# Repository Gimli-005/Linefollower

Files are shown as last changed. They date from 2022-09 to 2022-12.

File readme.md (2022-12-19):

# LineFollower
<br />
afbeelding
<br />
  
## specifications
<br />
microcontroller: ATmega32PU
<br />
motors: 50:1 Micro metal gear motor HP 6V
<br />
h-bridge: DRV 8835 Dual motor
<br />
sensors: QTR 8A sensor array
<br />
batteries: 1860 batteries
<br />
wireless communication: AZDelivery HM-10 Bluetooth Wireless RF Transceiver Module RS232 Seriële TTL 
<br />
distance sensor - motors: 140 mm
<br />
weight: 300 g
<br />
speed: 0.54
<br />

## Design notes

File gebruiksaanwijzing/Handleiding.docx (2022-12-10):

Handleiding

Syntheseproject

Linefollower

Robbe Malfroot
PBA-EM-3AM
971841rm

1. Opladen / vervangen batterijen

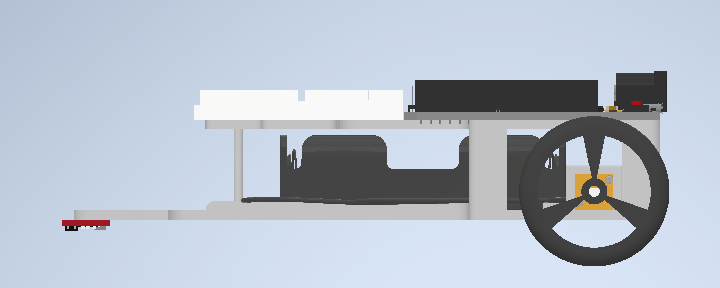
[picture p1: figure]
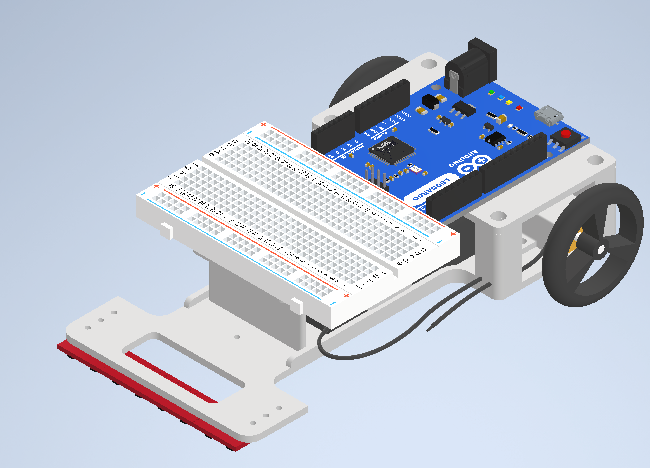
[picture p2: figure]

De batterijen kunnen vervangen worden door het bovenstaande arduino ondersteunig los te te koppelen. Waarbij we dan de batterijhouder van de linefollower kunnen halen. Om indien nodig de batterijen te vervangen. De batterijen kunnen opgeladen worden door een li-ion batterijlader, dat geschikt is voor 1860 batterijen op te laden.

2. Instellen HM-10 module

Het instellen van de HM-10 module gebeurt met AT-commando’s. Deze zijn terug te vinden in volgende link: https://people.ece.cornell.edu/land/courses/ece4760/PIC32/uart/HM10/DSD%20TECH%20HM-10%20datasheet.pdf

Installeer het programma “Bluetooth”. Open de Arduino IDE en open de seriële monitor. Hier plaatsen we de baudrate op 9600. Daarna stellen we de HM-10

module in met volgende commando’s:

- AT
- Controleert connectie: antwoord “OK”
- AT+NAME<uw naam> o Wijzigt naam naar “uwnaam”: antwoord “OK<uwnaam>”
- AT+BAUD<nummer>
- Wijzigt baudrate (voor ons naar nummer 4:9600): antwoord “OK<nummer>”
- AT-PIN<pincode> o Wijzigt pincode: antwoord “OK<pincode>”
- AT+RESET o Resets bluetooth module

Hierna is de MM-10 module ingesteld naar jouw voorkeur en klaar voor gebruik.

3. Verbinden bluetooth

Het verbinden met bluetooth gebeurd met de bluetooth app en de linefollower. Dit kan enkel nadat de bluetooth module is ingesteld bij stap 5.

Voor het instellen van HM-10 module gebeurt in volgende stappen:

1. Installeer de app op uw Android toestel via play store en type: Serial Bluetooth Terminal in.

2. Voorzie de linefollower van spanning

3. Verbind het Android toestel met de linefollower via bluetooth

a. Zoek hierbij naar de naam die je hebt ingesteld

b. Indien nodig, geef de code in die je hebt ingesteld

4. Open de Serial Bluetooth Terminal op het Android toestel

5. Ga naar “devices”

6. Druk op de ingestelde naam van jouw bluetooth module

a. Indien nodig, geef de code in die je hebt ingesteld

7. Ga naar “terminal”

8. Druk op het connect icoon rechts boven

a. In de terminal verschijnt:

i. Connecting…

ii. Connected

9. Hierna is de connectie bevestigd

10. Onderaan kunnen nu commando’s getypt worden en verzonden met het pijltje erna

a. De verzonden commando’s verschijnen in de terminal

b. Ook de antwoorden zullen te lezen zijn in de terminal

4. Gebruik van de linefollower

Eenmaal je verbonden bent met bluetooth door middel van stap 3 (Verbinden met bluetooth) kan je via bluetooth communiceren met de linefollower.

Daarna voor de linefollower te laten rijden moet eerst alle parameters ingesteld worden. Als de

sensoren moeten gekalibreerd worden.

Kalibreren

Voor de sensoren te kalibreren moet er in de seriële monitor via de computer of bluetooth module het commando worden getypt:

- “calibrate white”
- “calibrate black”

Indien het commando is doorgestuurd zal deze de waarden opslaan. Zorg er wel voor dat de linefollower op een volledige witte ondergrond staat om de witte waarden op te slaan en bij de zwarte waarden op een volledige zwarte ondergrond staat.

Rijden

Nu kunnen de parameters worden doorgestuurd aan de hand van de commando’s. Met het commando: “run” zal de line follower starten met rijden. Bij het commando “stop” zal deze stoppen met rijden.

Indien een commando wordt doorgestuurd die fout geschreven is of onjuist is zal er een message

verschijnen dat deze niet gevonden is, dus er kan niets kapot gaan door een fout commando door te

sturen.

De commando’s dat kunnen gegeven worden in bluetooth module:

- “run”:

=> Starten met rijden (dit kan ook met de knop gedaan worden).

- “stop”:

=> Stoppen met rijden.

- “debug”:

=> Tonen van de ingestelde parameters met de waarden.

- “calibrate”:

=> Calibreren van de sensoren.

- “set cycle ‘waarde”:

=> Set cycle naar ‘waarde’ (waarde moet cijfer zijn).

- “set power ‘waarde”:

=> Set power naar ‘waarde’ (waarde moet cijfer zijn).

- “set diff ‘waarde”:

=> Set diff naar ‘waarde’ (waarde moet cijfer zijn).

- “set kp ‘waarde”:

=> Set kp naar ‘waarde’ (waarde moet cijfer zijn).

- “set ki ‘waarde”:

=> Set ki naar ‘waarde’ (waarde moet cijfer zijn).

- “set kd ‘waarde”:

=> Set kd naar ‘waarde’ (waarde moet cijfer zijn).

Ingestelde waarden:

Tijdens het testen van de linefollower kwamen men bij deze instellingen de beste waarden uit:

- Cycle time: 1300
- Kp: 15
- Ki: 0
- Kd: 0.25
- Diff: 0.2
- Power: 100

Dit leverde een resultaat op met een snelheid van 0.54 m/s. Hierbij gaat de linefollower de lijn volgen met de ingestelde parameters.

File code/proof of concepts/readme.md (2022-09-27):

# Proof of Concepts

Een proof of concept is een combinatie van minimale hard- en software om eenvoudig aan te tonen dat iets werkt.  
Proof of concepts kunnen enerzijds als eerste poging dienen om een bepaald onderdeel van het project werkend te krijgen. Anderzijds kunnen ze tijdens het debuggen van het finale project dienen als test om eventuele hardware problemen te elimineren bij onduidelijke problemen.
<br />  
<br />
Een proof of concept bestaat uit
* een elektronisch schema (indien van toepassing)
* minimale code om de voorop gestelde zaken te demonstreren
* minimale uitleg / aandachtspunten
<br />
De elektronische schakelingen van de proof of concepts komen bij voorkeur overeen met deze van de uiteindelijke linefollower, zodat de code zonder aanpassingen op het finale project kan draaien.

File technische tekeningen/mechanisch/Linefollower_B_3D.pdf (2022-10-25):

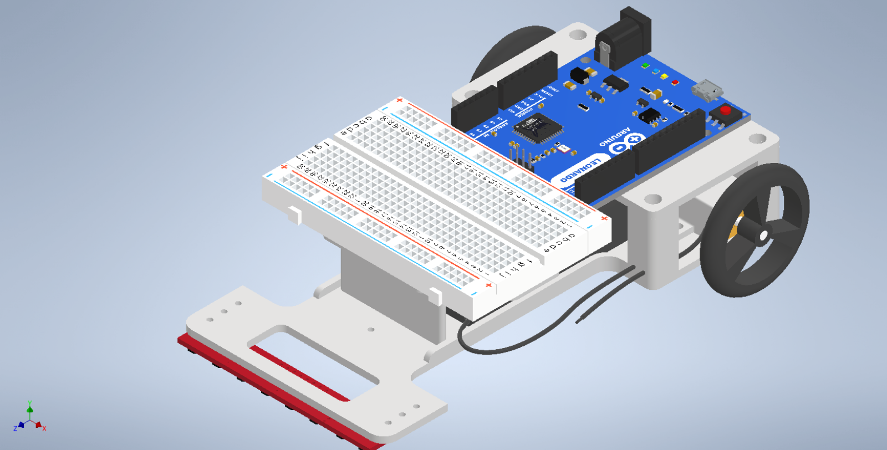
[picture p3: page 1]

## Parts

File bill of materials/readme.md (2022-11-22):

## bill of materials
<br />

|volgnummer|naam|omschrijving|nieuw/recup|kostprijs/stuk|aantal|subtotaal|
|---|----|---|---|---|---|---|
| 1| 50:1 Micro metal gear motor HP 6V  | | Nieuw | €20,41 |  2 | €40,82 |
| 2| QTR 8A Sensor array | | Nieuw | €10,18 | 2 | €20,36 |
| 3| Wheels 40*8mm  | | Nieuw | €5,06 | 2 | €10,12 |
| 4| Batterijen 18650  | | Nieuw | €15,09 |  6 | €15,09 |
| 5| Batterijhouder voor 18650  | | Nieuw |  €5,39 |  1 | €5,39 |
| 6| H-brug  DRV8835 | Voor besturing wielen |  Nieuw | €14,27 |  1 |  €14,27 |
| 7| Communicatie HC-05  | | Nieuw | €6,99 + €2,25  |  1 |  €9,25 |
| 8| Arduino Leonardo | | Nieuw | €25,52  | 1 | €25,52 |
| 9| Bouten M2/M5 | | recup | |  1 | |
| 10| Batterijlader 18650 | |  Nieuw | €15,02 |  1 | €15,02 |
| 11| Moeren M2/M5 | | recup | | 1 | |
| 13| printplaatje 5cmx7cm  | | nieuw | 1 | 1  | €0.99 |
| 14| Transportkosten | | | | | €36,00 |
| 15| | | | | | |
| 16| Totaal | | | | | €176,65 |

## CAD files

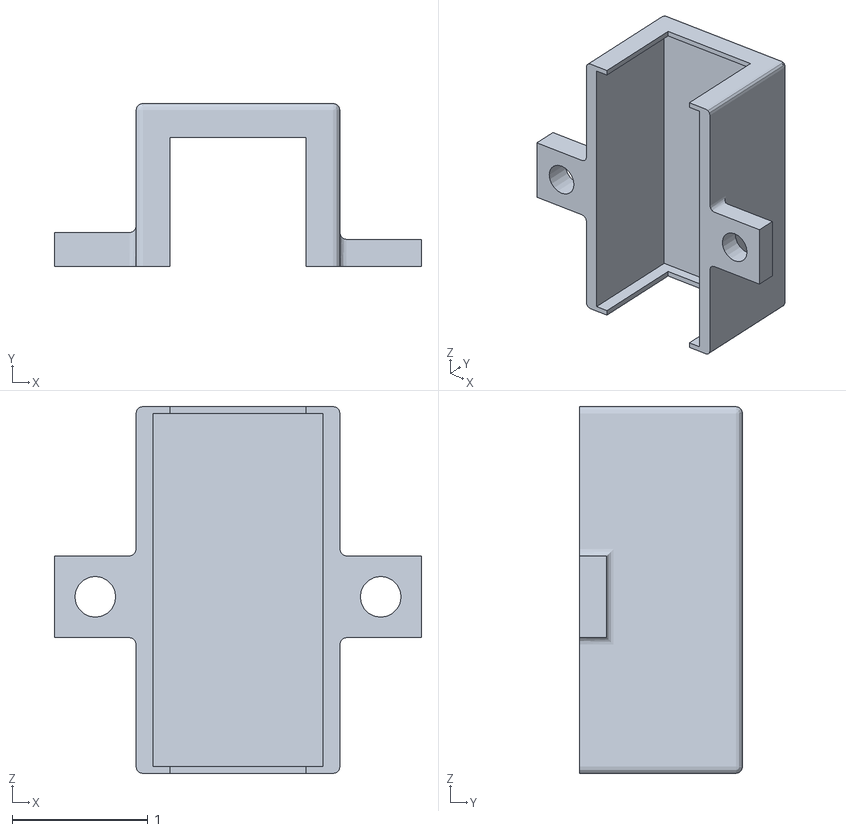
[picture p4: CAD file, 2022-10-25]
technische tekeningen/mechanisch/Ondersteuning motor.stl
2.70 x 1.20 x 2.70

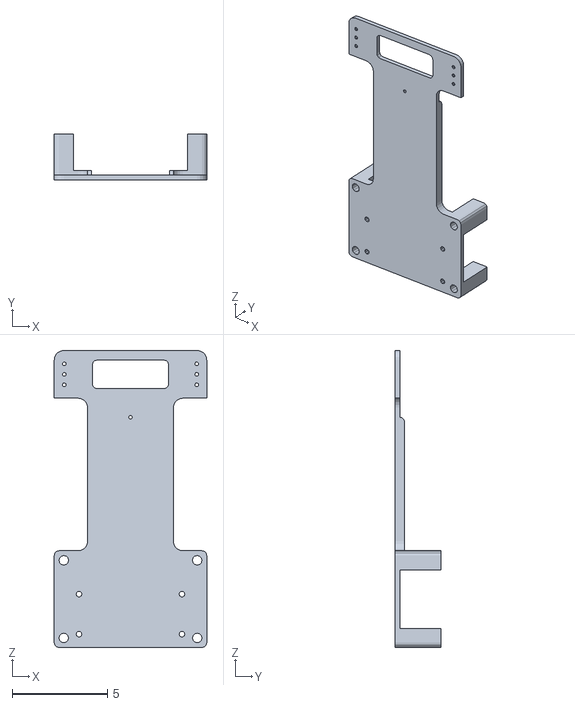
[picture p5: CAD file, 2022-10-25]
technische tekeningen/mechanisch/Chasis Linefollower_verbeterd.stl
8.00 x 2.40 x 15.6

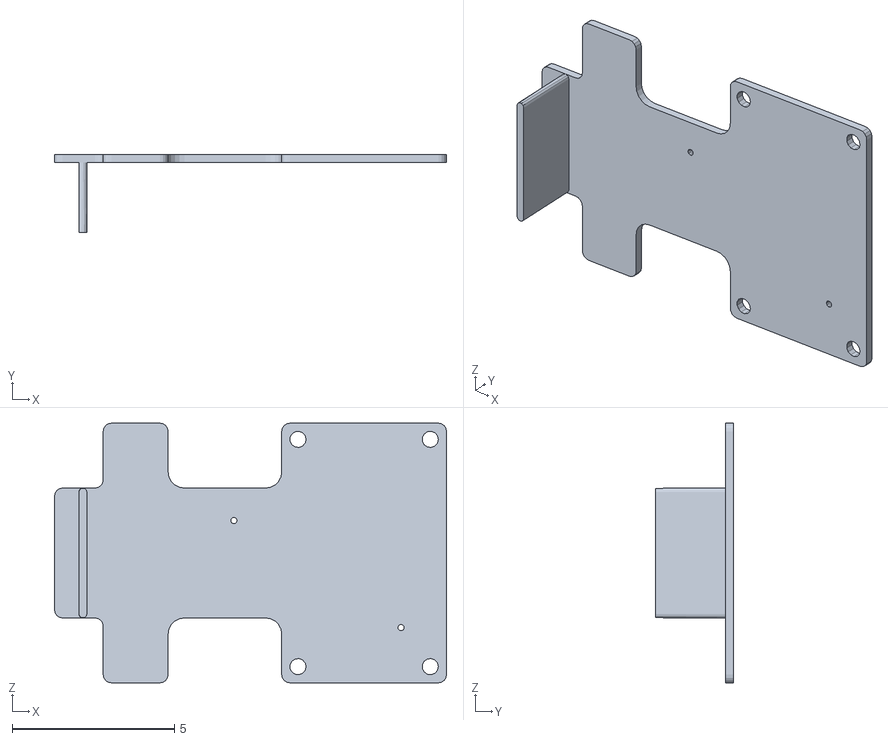
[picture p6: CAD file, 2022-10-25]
technische tekeningen/mechanisch/Arduino-ondersteuning.stl
12.1 x 2.40 x 8.00

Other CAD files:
technische tekeningen/mechanisch/Arduino-ondersteuning.ipt
technische tekeningen/mechanisch/Linefollower_B.idw
technische tekeningen/mechanisch/Samenstelling aandrijving.iam
technische tekeningen/mechanisch/Wiel.ipt
technische tekeningen/mechanisch/batteijhouder_1.ipt

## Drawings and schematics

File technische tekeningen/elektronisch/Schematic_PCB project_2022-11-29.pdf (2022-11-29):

## U1HC⁻05

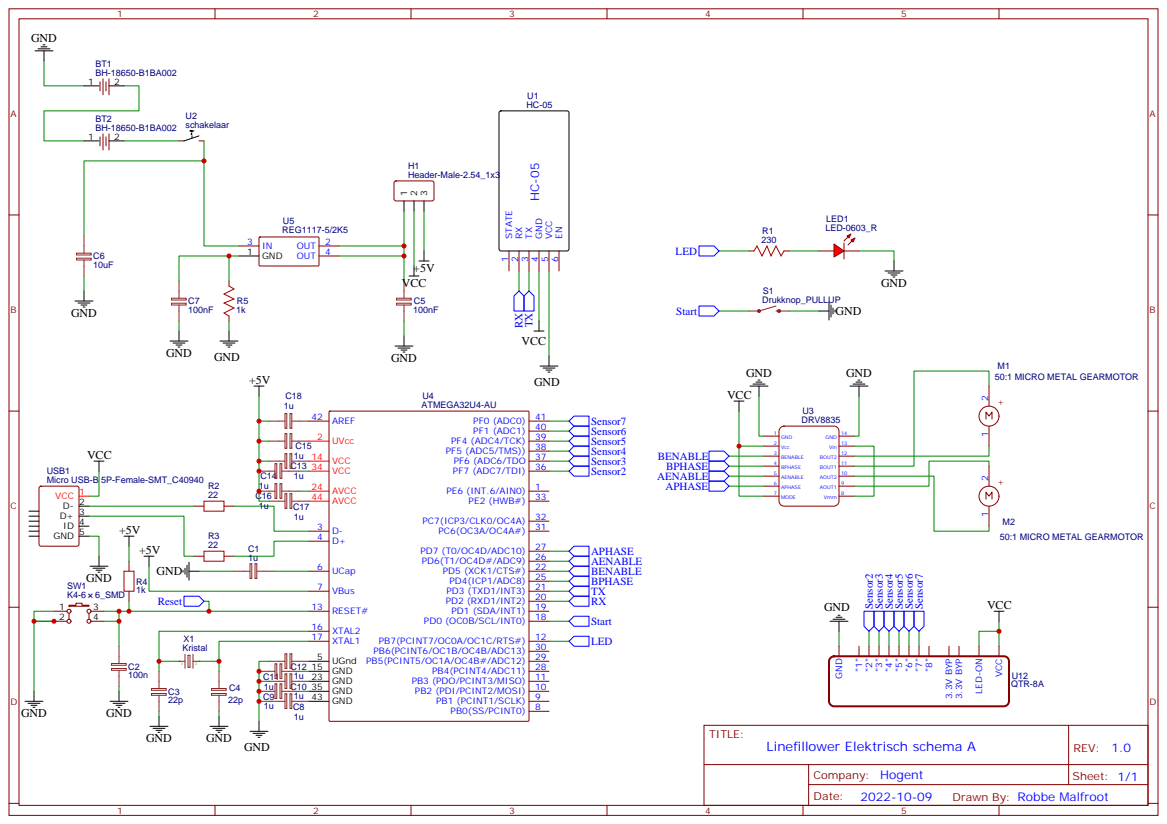
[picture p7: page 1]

PB7(PCINT7/OC0A/OC1C/RTS#) 12
PB2 (PDI/PCINT2/MOSI) 10 PB3 (PDO/PCINT3/MISO) 11 PB4(PCINT4/ADC11) 28 PB5(PCINT5/OC1A/OC4B#/ADC12) 29 PB6(PCINT6/OC1B/OC4B/ADC13) 30

Drawn By: Robbe Malfroot

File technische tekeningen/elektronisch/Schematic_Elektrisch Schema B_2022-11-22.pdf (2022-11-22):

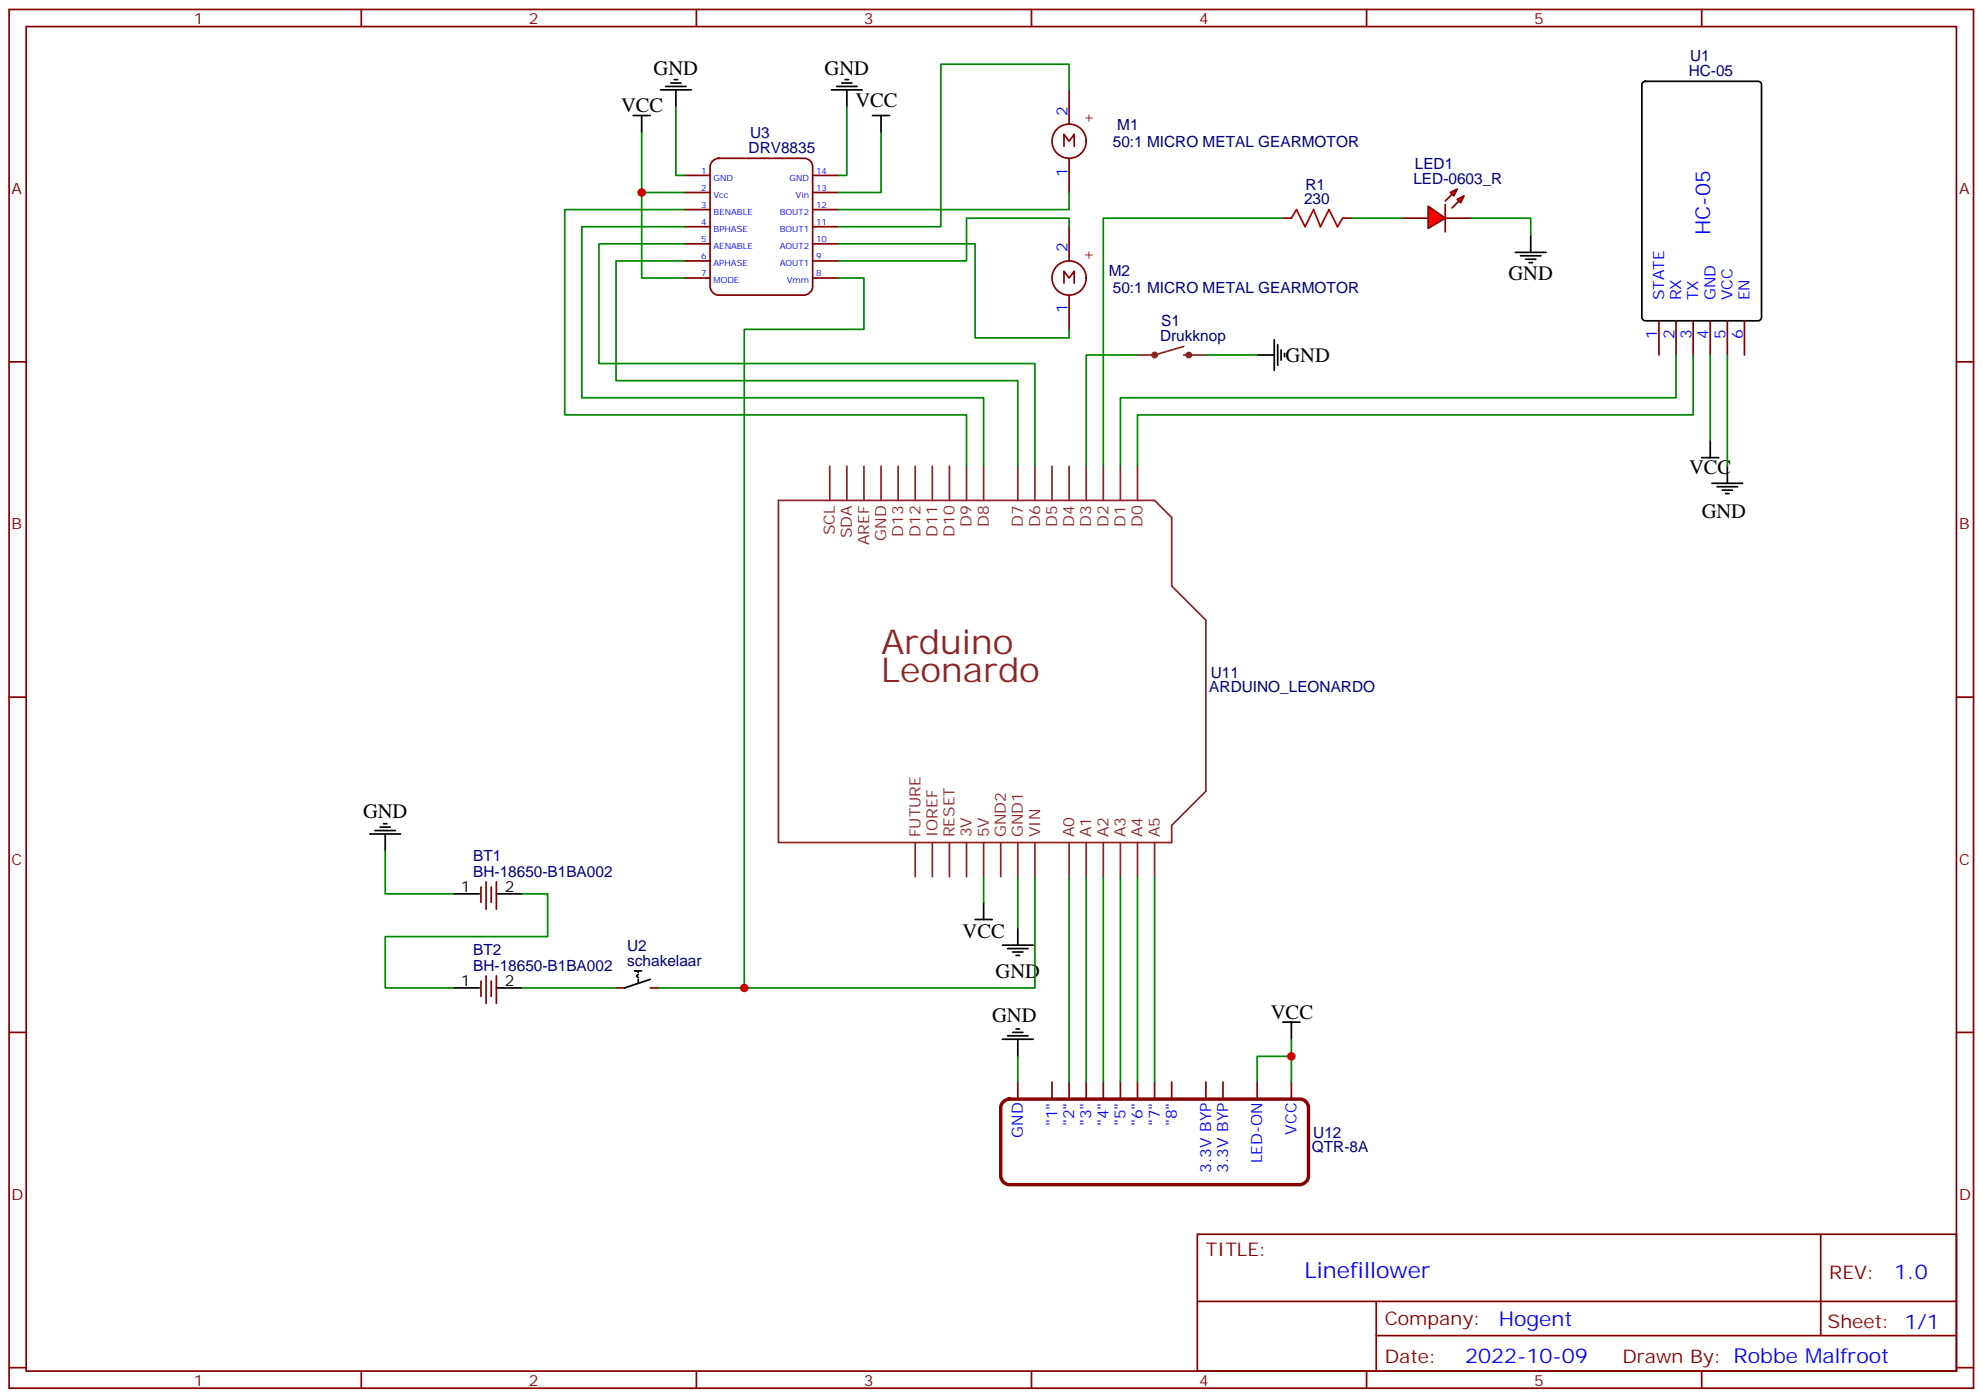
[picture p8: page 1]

Drawn By: Robbe Malfroot

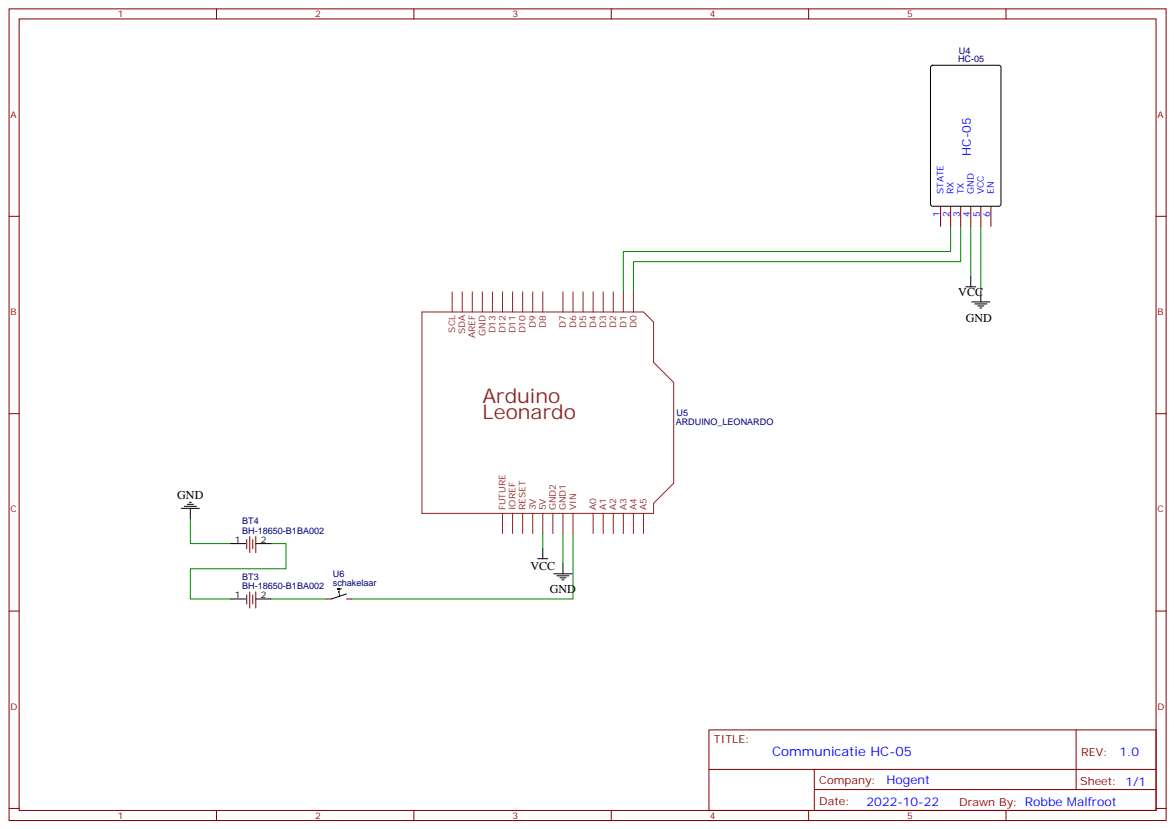
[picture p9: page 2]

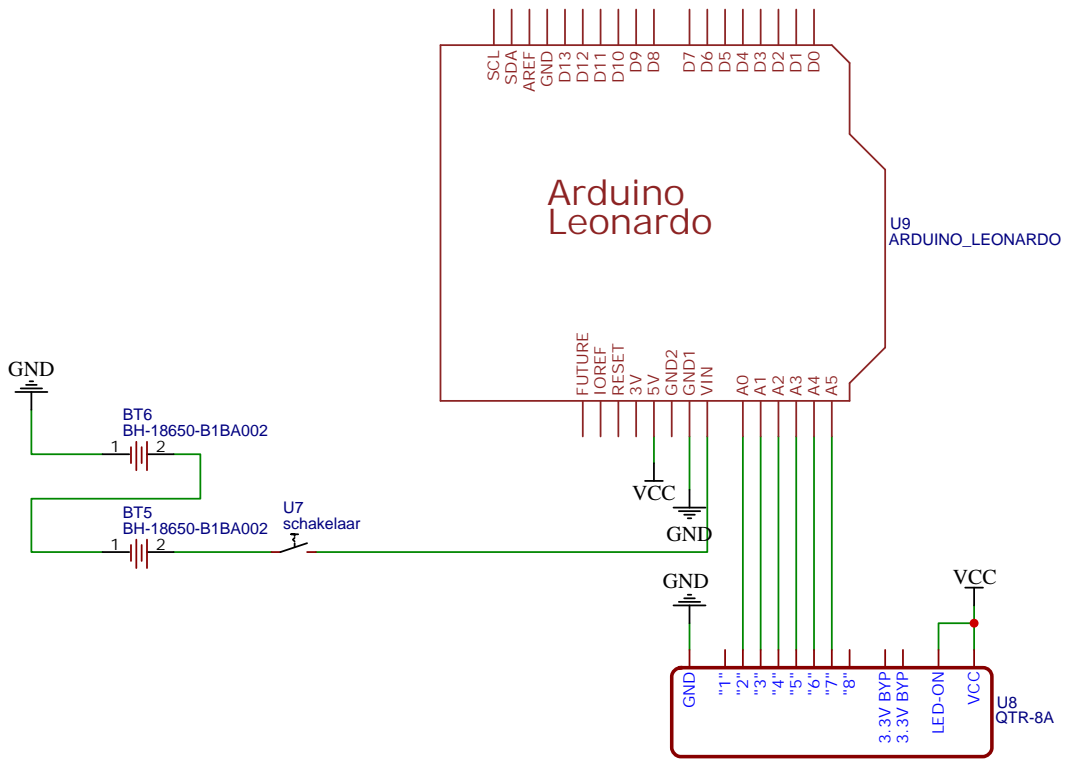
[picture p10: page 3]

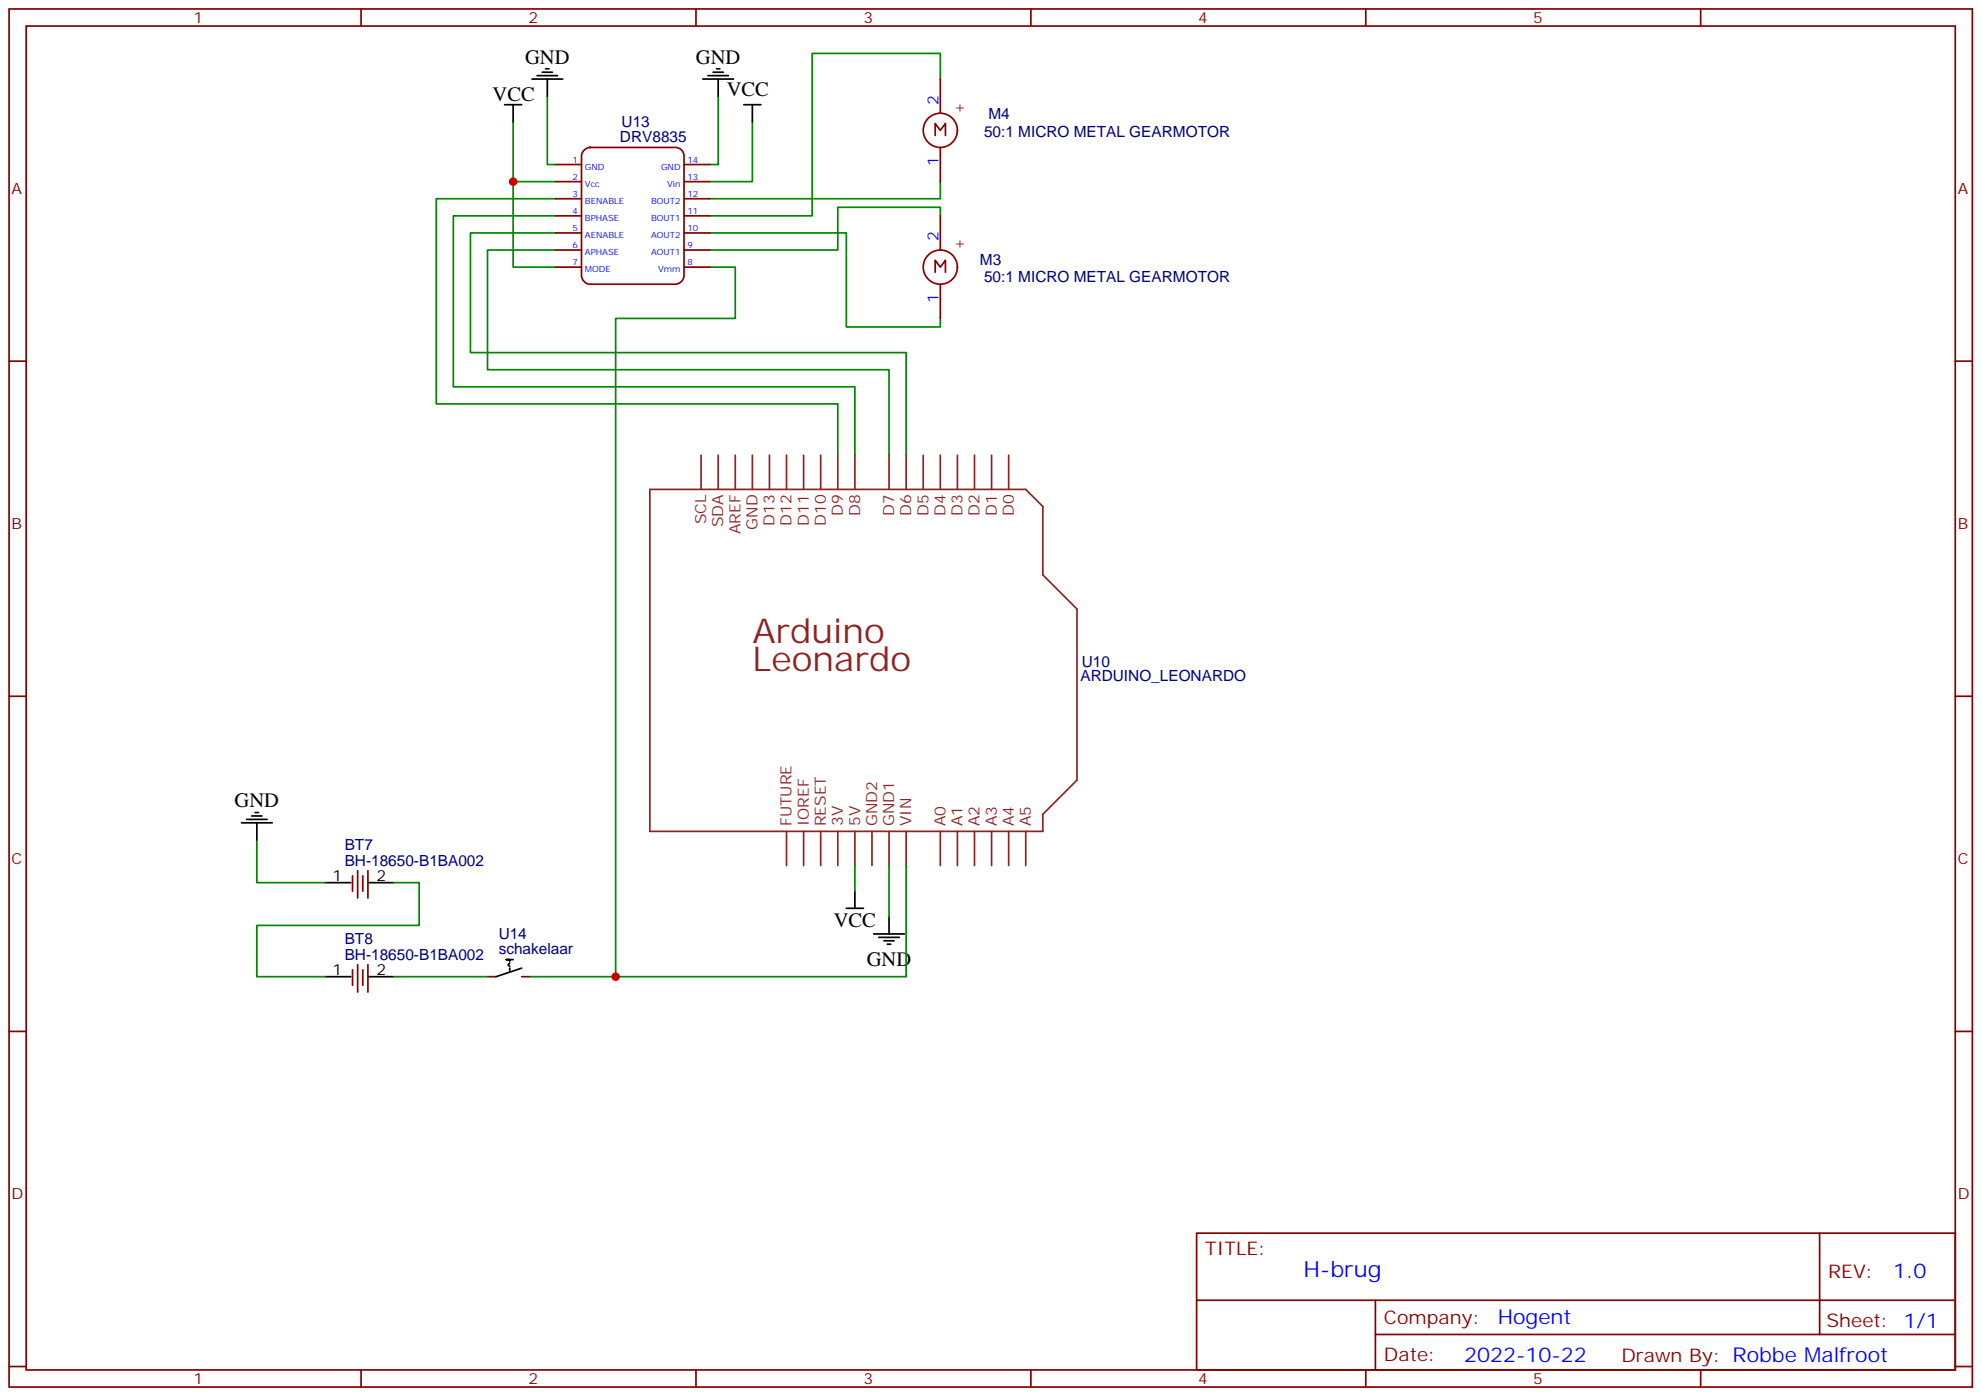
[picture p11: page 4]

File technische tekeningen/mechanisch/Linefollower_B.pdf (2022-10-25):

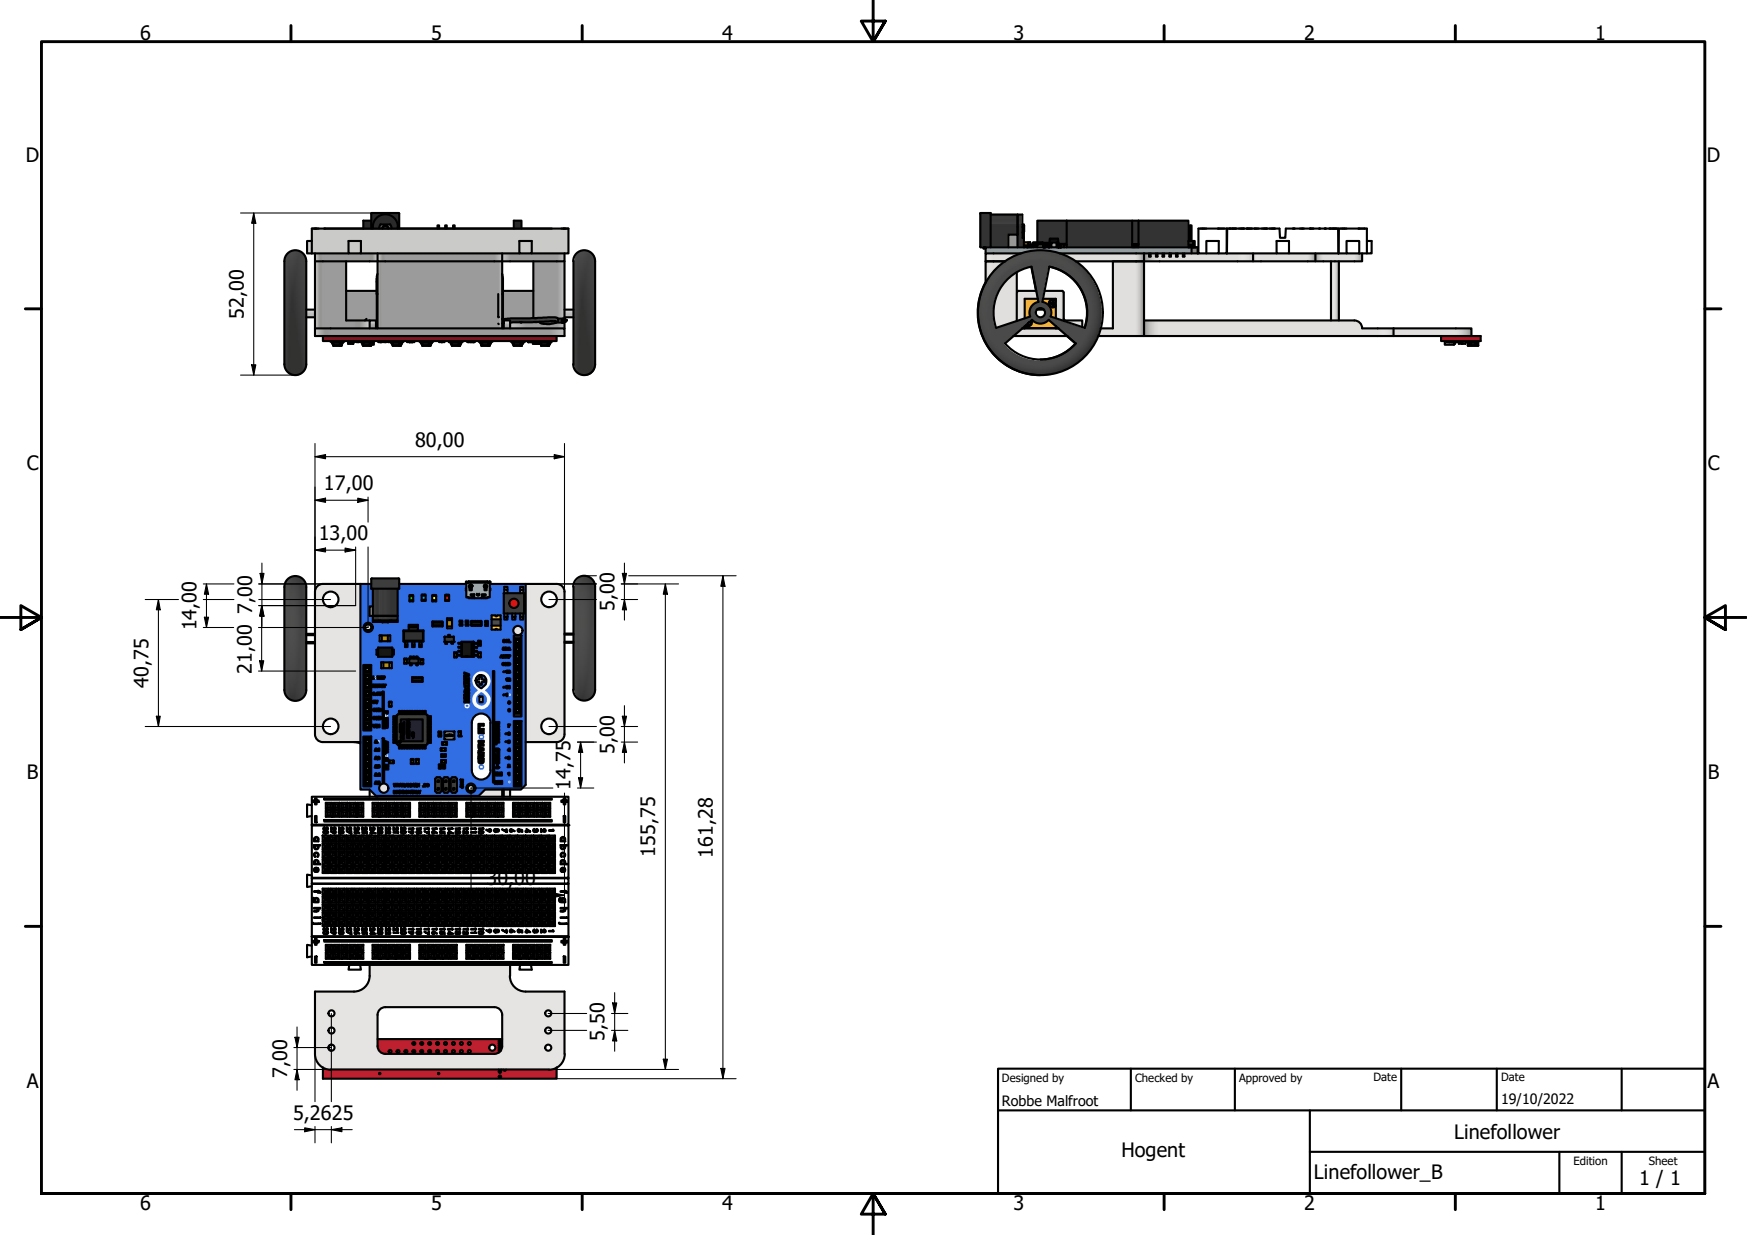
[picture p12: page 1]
Robbe Malfroot; Designed by; Checked by; Approved by; Date

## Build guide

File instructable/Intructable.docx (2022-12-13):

Instructable

Syntheseproject

Linefollower

Robbe Malfroot
PBA-EM-3AM
971841rm

## Benodigdheden

Onderstaand zijn alle benodigdheden voor het maken van een linefollower zonder PCB. De specificaties en de datasheets van de gebruikte onderdelen staan gedetailleerd beschreven in de Bill of materials.

| Stuk nr. | aantal | naam
Bron
| 1 | 2 | Batterij
| 2 | 1 | Batterijhouder
| 3 | 1 | Charger
H-brug
| 4 | 2 | H-brug DRV 8835
Motoren
| 5 | 2 | Micro gear motor
| 6 | 2 | Polulu wielen
Communicatie
| 7 | 1 | Bluetooth HM-10/HC-05
Microcontroller
| 8 | 1 | controller
Sensoren
| 9 | 1 | QTR-8A
Body
| 10 | 1 | Breadboard
| 11 | | Male-Female headers
| 12 | | Male - Male headers
| 13 | 1 | Schakelaar
| 14 | 1 | Body
| 15 | 4 | Bout M5
| 16 | 1 | Drukknop
| 17 | 4 | Bout M2
Gereedschap
| 18 | 1 | Soldeerbout
| 19 | 1 | Soldeertin
| 20 | 1 | Desoldeerlint
| 21 | 1 | Striptang
| 22 | 1 | Kniptang

## Breadboard

Binnen het project is er gekozen voor een breadboard om de verschillende connecties en componenten gemakkelijker te kunnen aansluiten en demonteren. Het nadeel is wel echter dat het ook gemakkelijker los komt omdat niet vast gemaakt zijn. Bij het aansluiten van de verschillende componenten zal er meer bekabeling gebruikt worden, waardoor dit minder overzichtelijk is. Als laatste kan een breadboard goed zijn voor het te testen. Omwille als men een printplaat gaat solderen dit bevestigd is aan het printplaat waardoor als men een fout maakt dat je dit dan ook moet aanpassen.

## Assemblage

Er is gebruik gemaakt van een 3d-printer voor het maken van de chassis.

Omdat 3D-materiaal een licht materiaal is als goedkoop is. Dat gemakkelijk indien bewerkbaar is.

Voor men de assemblage in elkaar monteren, moet eerst alle benodigde componenten gesoldeerd zijn met de benodigde bekabeling of pinnen.

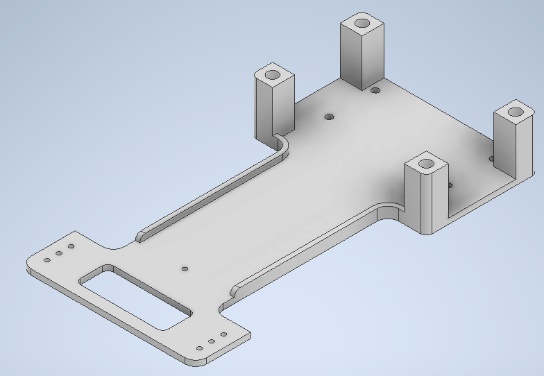
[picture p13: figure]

Vooraan de chassis is er voorzien van M2 gaten voor de QTR-8 sensor te bevestigen. Dit kan gemonteerd worden door M2 bouten met moeren om de sensor vast te maken. Alsook wordt een speling voorzien voor de analoge pinnen op de sensor te kunnen aansluiten op de arduino. Daarna wordt er nog een gat voorzien, waarbij een M4-bout is bevestigd. Deze zal er voor zorgen de hoogte te regelen hoe ver de sensor van de grond mag komen.

Voordat we de motoren gaan bevestigen aan de chassis zal eerst de aangekochte wielen op de motoren bevestigd worden.

Figuur 1: Chassis

Vervolgens zullen de bracket die op de micro gear motors geschoven worden en gemonteerd worden aan de chassis bij de benodigde gaten die aan de achterkant van de chassis bevinden.

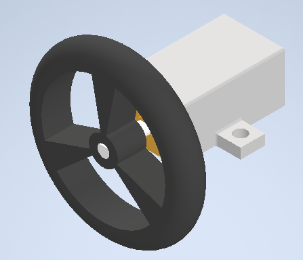
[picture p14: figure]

Als laatste zal de batterijhouder met de voorziene LI-batterijen (1860 batterijen) geplaatst worden op de chassis waarna het ondersteunstuk voor de arduino deze klem zet, zodat deze niet meer weg kan.

Figuur 2:Micro-gear-motor, wiel en bracket

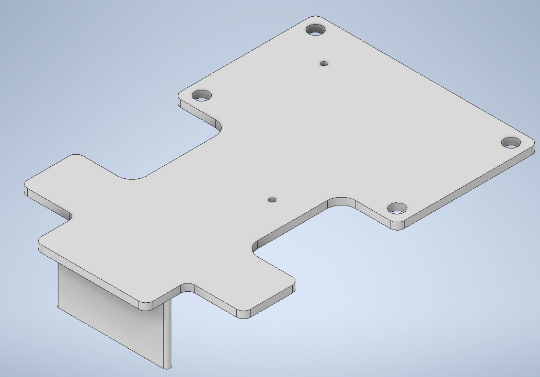
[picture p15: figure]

Daarna zal de arduino vast gemaakt worden door M2 bouten en moeren op de ondersteuning van de arduino.

De volgende stap zal de ondersteunstuk van de arduino geplaatst worden op de chassis zijn vier ondersteuners. Waarbij deze bevestigd worden x4 M5-bouten en moeren.

Als laatste zal de breadboard op deze ondersteuning geplaatst worden waarbij men de nodige aansluitingen moeten voorzien op het elektrisch schema plan B. Waarna de breadboard dan bevestigd wordt door paar kabelbinders.

Figuur 3: Ondersteuning arduino

Het uploaden van het programma gebeurt door de arduino aan te sluiten aan u pc aan de hand van een USB-kabel. Waarbij men dan de Finaal code van de linefollower gaan uploaden.

De kalibratie van de sensoren gebeurt door de sensor boven een wit blad te houden en de volgende commando in te voeren in de serial Bluetooth terminal:

- calibrate white
  - Waarna men een boodschap terug krijgen dat calibrate white is complete.

Dit zal men dan ook doen boven een zwart vlak met de volgende commando:

- Calibrate black
  - Waarna men een boodschap terug krijgen dat calibrate black is complete.

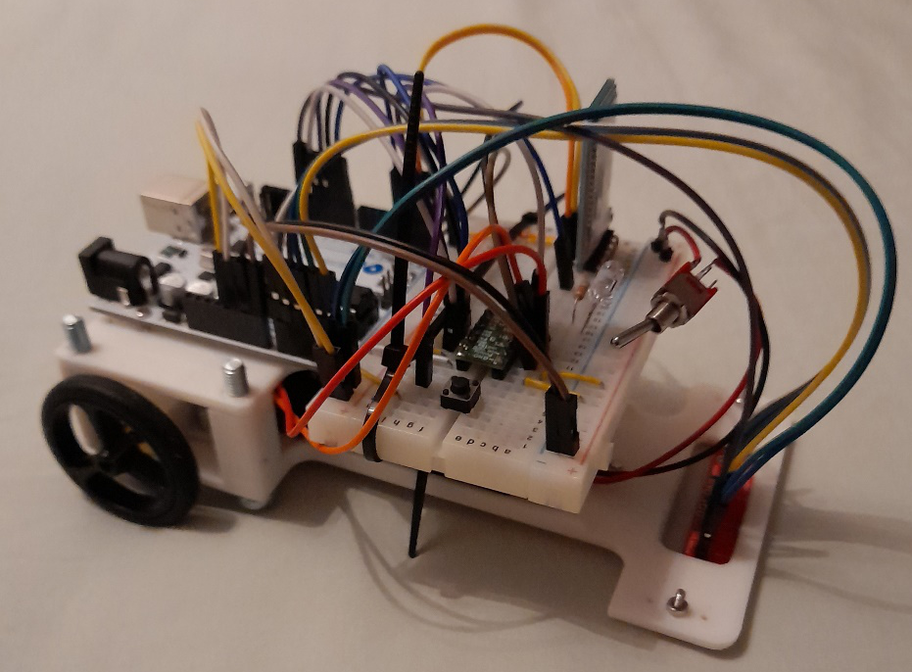
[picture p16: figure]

Hierna kan de linefollower gestart worden en de nodige parameters in geven voor deze te laten rijden.

Figuur 4: Totaal linefollower

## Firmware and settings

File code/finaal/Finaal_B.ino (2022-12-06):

#include "SerialCommand.h"
#include "EEPROMAnything.h"

#define SerialPort Serial
#define Baudrate 9600 

#define  BIN2 10 // MotorRightForward (Benable)
#define  BIN1 11 // MotorRightBackward (Bphase)
#define  AIN2 3 // MotorLeftForward(Aenable)
#define  AIN1 9 // MotorLeftForward (Aphase)

SerialCommand sCmd(SerialPort); // SerialCommand object declaration 
bool debug;
bool run;
//bool stop; 
unsigned long Current;
unsigned long previous;
unsigned long calculationTime;
unsigned long Difference; 
unsigned long cycleTime = 2500;
float iTerm = 0;
float lastErr; 

//sensoren
const int sensor[] = { A5, A4, A3, A2, A1, A0}; 

const int led = 8;
const int Drukknop = 2; 


// EEPROM opgeslagen parameteres 
struct param_t
{
  unsigned long cycleTime; 
  /* andere parameters die in het eeprom geheugen moeten opgeslagen worden voeg je hier toe ... */
  int black[6];
  int white[6];
  int power; 
  float diff;
  float kp;  
  float ki; 
  float kd;
} params;

  int normalised[6];
  float debugPosition;
  float output;

void setup()
{
  SerialPort.begin(Baudrate); // set serial baudrate at 115200

  sCmd.addCommand("set", onSet);
  sCmd.addCommand("debug", onDebug);
  sCmd.addCommand("calibrate", onCalibrate);
  sCmd.addCommand("run", onRun);
  sCmd.addCommand("stop", onStop); 
  sCmd.setDefaultHandler(onUnknownCommand);
  EEPROM_readAnything(0, params);

  pinMode(13, OUTPUT);
  digitalWrite(13, HIGH);

  pinMode(2, OUTPUT); 
  pinMode(BIN2, OUTPUT);
  pinMode(BIN1, OUTPUT);
  pinMode(AIN2, OUTPUT);
  pinMode(AIN1, OUTPUT);
  
  SerialPort.println("ready");
}

void loop()
{
  sCmd.readSerial(); // listen and process serial commands
  
  unsigned long current = micros();
  if (current - previous >= params.cycleTime)
  {
    previous = current;
    /* code die cyclisch moet uitgevoerd worden programmeer je hier ... */
    //SerialPort.print("normalised values: ");
    for (int i = 0; i < 6; i++)
    {
      normalised[i] = map(analogRead(sensor[i]), params.black[i], params.white[i], 0, 1000); 
    }

    float position = 0; // positie bepalen sensoren 
    int index = 0; // zwartste sensor bepalen

    for(int i = 1; i < 6; i++) if (normalised[i] < normalised[index]) index = i; // nieuwe zwartste sensor zoeken 
    //SerialPort.println(normalised[index]);

    if (normalised[index]); 

    if (index == 0) position = -30; 
    else if (index == 5) position = 30;
    else
    {
      int sensor_nul = normalised[index];
      int sensor_min_een = normalised[index-1];
      int sensor_plus_een = normalised[index+1];

      float b = sensor_plus_een - sensor_min_een;  // b berekenen 
      b = b / 2; 

      float a = sensor_plus_een - b - sensor_nul; 

      position = -b / (2 * a); 
      position += index;
      position -= 2.5;

      position *= 9.525;      
    }
    debugPosition = position; 
    
    /* normaliseren en interpoleren sensor */
    /* bereken error = setpoint - positie */
    float error = -position;

    /* proportioneel regelen */
    float output = error * params.kp;


    // integrerend regelen 
    iTerm += params.ki * error;
    iTerm = constrain(iTerm, -510, 510);
    output += iTerm;

    // differentierend regelen
    output += params.kd * (error - lastErr);
    lastErr = error; 

    // aansturen motoren & begrenzen
    output = constrain(output, -510, 510); 
    
    int powerLeft = 0;
    int powerRight = 0;
    
    if (run) if (output >= 0)
    {
      powerLeft = constrain(params.power + params.diff * output, -255, 255); 
      powerRight = constrain(powerLeft - output, -255, 255); 
      powerLeft = powerRight + output; 
    }
    else
    {
      powerRight = constrain(params.power - params.diff * output, -255, 255); 
      powerLeft = constrain(powerRight + output, -255, 255); 
      powerRight = powerLeft - output;
    }

   /* SerialPort.print("powerLeft");
    SerialPort.println(powerLeft);
    
    SerialPort.print("powerRight"); 
    SerialPort.println(powerRight);
    */
    //H-brug waardes wegschrijven 
    
    analogWrite(AIN2, powerLeft > 0 ? powerLeft : 0);
    analogWrite(AIN1, powerLeft < 0 ? -powerLeft : 0);
    analogWrite(BIN2, powerRight > 0 ? powerRight : 0);
    analogWrite(BIN1, powerRight < 0 ? -powerRight : 0);
  } 

  unsigned long difference = micros() - current;
  if (difference > calculationTime) calculationTime = difference;
}

void onRun()
{
  run =true;
  digitalWrite(led, HIGH); 
}

void onStop()
{
  run =false; 
  digitalWrite(led, LOW);
}

void onCalibrate()
{
  char* param = sCmd.next();

  if (strcmp(param, "black") == 0)
  {
    SerialPort.print("start calibrating black... ");
    for (int i = 0; i < 6; i++) params.black[i] = analogRead(sensor[i]);   
    SerialPort.println("done");
    
  }
  else if (strcmp(param, "white") == 0)
  {
    SerialPort.print("start calibrating white... ");
    for (int i = 0; i < 6; i++) params.white[i] = analogRead(sensor[i]);   
    SerialPort.println("done");
  }
  EEPROM_writeAnything(0, params);
}

void onSet()
{
  char* param = sCmd.next();
  char* value = sCmd.next();


  // ki
  if (strcmp(param, "cycle") == 0)
  {
    long newCycleTime = atol(value);
    float ratio = ((float) newCycleTime) / ((float) params.cycleTime);

    params.ki *= ratio;
    params.kd /= ratio; 

    params.cycleTime = newCycleTime;
  }
  
  else if (strcmp(param, "ki") == 0)
  {
    float cycleTimeInSec = ((float) params.cycleTime) / 1000000;
    params.ki = atof(value) * cycleTimeInSec;
  }
  else if (strcmp(param, "kd") == 0)
  {
    float cycleTimeInSec = ((float) params.cycleTime) / 1000000;
    params.kd = atof(value) / cycleTimeInSec;
  }


  if (strcmp(param, "cycle") == 0) params.cycleTime = atol(value); // if 
  else if (strcmp(param, "power") == 0) params.power = atol(value); 
  else if (strcmp(param, "diff") == 0) params.diff = atof(value);
  else if (strcmp(param, "kp") == 0) params.kp = atof(value);
  else if (strcmp(param, "ki") == 0) params.ki = atof(value);
  else if (strcmp(param, "kd") == 0) params.kd = atof(value);
    
    /* parameters een nieuwe waarde geven via het set commando doe je hier ... */
  EEPROM_writeAnything(0, params);
}

void onDebug()
{
  SerialPort.print("cycle time: ");
  SerialPort.println(params.cycleTime);
  
  /* parameters weergeven met behulp van het debug commando doe je hier ... */
  SerialPort.print("black: ");
  for (int i = 0; i < 6; i++)
  {
    SerialPort.print(params.black[i]);
    SerialPort.print(" ");
  }
  SerialPort.println(" ");

  SerialPort.print("white: ");
  for (int i = 0; i < 6; i++)
  {
    SerialPort.print(params.white[i]);
    SerialPort.print(" ");
  }
  SerialPort.println(" ");

  SerialPort.print("normalised: ");
  for (int i = 0; i < 6; i++)
  {
    SerialPort.print(normalised[i]);
    SerialPort.print(" "); 
  }
  SerialPort.println(" ");

  SerialPort.print("output: ");
  SerialPort.println(output); 

  SerialPort.print("power: ");
  SerialPort.println(params.power);
  SerialPort.print("diff: ");
  SerialPort.println(params.diff);
  SerialPort.print("kp: ");
  SerialPort.println(params.kp);

  float cycleTimeInSec = ((float) params.cycleTime) / 1000000;
  float ki = params.ki / cycleTimeInSec;
  SerialPort.print("ki: ");
  SerialPort.println(ki);

  float kd = params.kd * cycleTimeInSec;
  SerialPort.print("kd: ");
  SerialPort.println(kd);
  
 SerialPort.print("Normalised Values Sensoren: ");
  for (int i = 0; i < 6; i++)
  {
    normalised[i] = map(analogRead(sensor[i]), params.black[i], params.white[i], 0, 1000);
    SerialPort.print(normalised[i]);
    SerialPort.print(" ");
  }
  SerialPort.println();

  SerialPort.print("Calculation Time: ");
  SerialPort.println(calculationTime);
  calculationTime = 0;
}

void onUnknownCommand(char *command)
{
  SerialPort.print("unknown command: \"");
  SerialPort.print(command);
  SerialPort.println("\""); 
}

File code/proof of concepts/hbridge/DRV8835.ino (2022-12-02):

int IN2= 11; //BENABLE
int IN1=  10; //BPHASE
int IN4= 3; //AENABLE
int IN3 = 9; //APHASE



void setup()
{
  pinMode(IN1, OUTPUT);
  pinMode (IN2, OUTPUT);

  pinMode(IN3, OUTPUT);
  pinMode (IN4, OUTPUT);
    
}

void loop()
  {
// Voorwaarts
    for (int i = 0; i <= 255; i++)
    {
      analogWrite(IN1, i);
      analogWrite(IN2, 0);
      analogWrite(IN3, 0);
      analogWrite(IN4, i);
      delay(10);
    }
    for (int i = 255; i >= 0; i--)
    {
      analogWrite(IN1, i);
      analogWrite(IN2, 0);
      analogWrite(IN3, 0);
      analogWrite(IN4, i);
      delay(10);
    }

    delay(2000);

    // Achterwaarts
    for (int i = 0; i <= 255; i++)
    {
      analogWrite(IN1, 0);
      analogWrite(IN2, i);
      analogWrite(IN3, i);
      analogWrite(IN4, 0);
      delay(10);
    }
    for (int i = 255; i >= 0; i--)
    {
      analogWrite(IN1, 0);
      analogWrite(IN2, i);
      analogWrite(IN3, i);
      analogWrite(IN4, 0);
      delay(10);
    }

    delay(2000);

    // Links
    for (int i = 0; i <= 255; i++)
    {
      analogWrite(IN1, i);
      analogWrite(IN2, 0);
      analogWrite(IN3, i);
      analogWrite(IN4, 0);
      delay(10);
    }
    for (int i = 255; i >= 0; i--)
    {
      analogWrite(IN1, i);
      analogWrite(IN2, 0);
      analogWrite(IN3, i);
      analogWrite(IN4, 0);
      delay(10);
    }

    delay(2000);

    // Rechts
    for (int i = 0; i <= 255; i++)
    {
      analogWrite(IN1, 0);
      analogWrite(IN2, i);
      analogWrite(IN3, 0);
      analogWrite(IN4, i);
      delay(10);
    }
    for (int i = 255; i >= 0; i--)
    {
      analogWrite(IN1, 0);
      analogWrite(IN2, i);
      analogWrite(IN3, 0);
      analogWrite(IN4, i);
      delay(10);
    }
  }
